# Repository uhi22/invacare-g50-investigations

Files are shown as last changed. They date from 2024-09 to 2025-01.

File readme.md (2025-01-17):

# Invacare G50 Investigations

Investigating an electric wheel chair

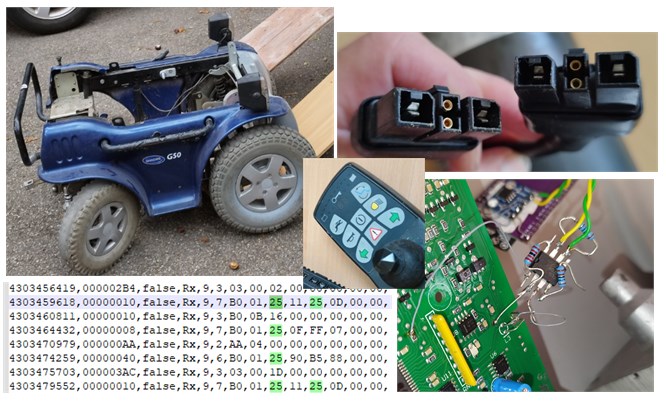
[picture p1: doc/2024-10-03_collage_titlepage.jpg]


## Progress

### 2025-01-07: DX-DASH Generation 2 ready for testing

The DX-DASH generation 2 consists of a board containing an STM32 controller, designed in KiCad,
a housing designed in FreeCad and the software designed in the STM CubeIDE.
The DX-DASH gen2 is controlling the Power Module, using either joystick or drive pedal and
direction switch.

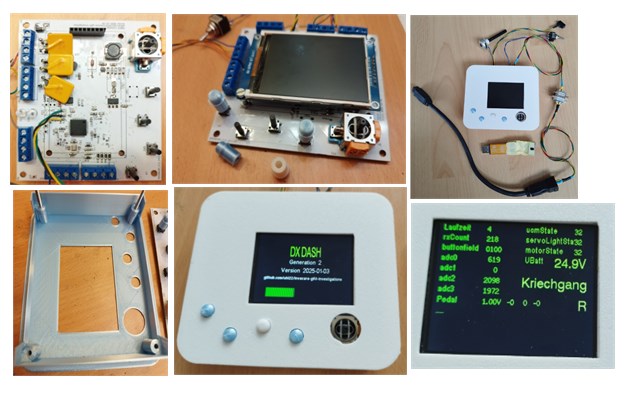
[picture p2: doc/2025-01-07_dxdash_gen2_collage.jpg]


[Instruction manual](doc/2025-01-06_DXDASH_installation_und_bedienung.md)

### 2024-10-15: STM32 simulates the UCM and the SLM

Simulating the UCM and the ServoLightModule, the STM32 is able to control
the motor speed directly.

### 2024-10-11: STM32 as UCM-replacement controls all functionality

The STM32 as UCM replacement controls a lot of functionality:
- Wakeup the other modules via the DXBUS
- Control the low beam light and the flashers
- Switch the power module into driving mode and back to idle mode
- Drive motor forwards and backwards using analog joystick input
- Turn the steering servo left and right using analog joystick input
- Send the power module and servo light module to sleep

### 2024-10-02: First spin

The STM32 sends all CAN messages to make the motor spin.

### 2024-09-30: Steering reacts

By sending some half-way proper CAN messages from the STM32 UCM replacement, the servo can be controlled to right-turn.
The motor disables the brake, but does not spin yet. It blinks 12 times.

### 2024-09-26: Controlling the lights works

Using the STM32 "blue pill" and a CAN transceiver, we control the lights via CAN. Due to the disconnected UCM,
the motor controller is stuck in state 0C, and the ServoLightModule in state 0. But nevertheless, low beam and
the turn indicators can be perfectly controlled with a 20ms message "0x040 B0 14 xx".
The ServoLightModule works even with very low battery voltage of 10V in this situation.

### 2024-09-24: STM32 interprets some network variables

Using the STM32 and attached display, we decode some network variables out of the CAN messages,
and show them on the display. 

## Goals

1. Understand the communication on the DX-BUS
2. Replace the original joystick ("UCM") by a self-made box which can control the motor, the lights and the steering.
3. Replace the UCM and the ServoLightModule by a self-made box to control only the motor.

## Pinout of the Power Module

The "Power Module" is a DX-PMB2-SAS, producer "Dynamic Controls", this seems to be the same as the DX-PMB2 mentioned in Ref1.

## Bus Communication

The "DXBUS" consists of four pins:
* Ground
* 24V
* CANH
* CANL

The ground and 24V are directly connected to the battery pins of the power module.

CAN bit time is 9.5µs, this means the CAN baud rate is 105.26 kBaud.
This baud rate can be created (according to STM32 cube IDE) with prescaler=57, T1=3, T2=2, SJW=1, TQ=1583.3ns, bittime=9500ns, 6 TQ per bit, inputClock=36MHz.

### CAN messages

UCM transmit messages (found by adding a separate CAN transceiver to the UCMs CAN_TX line):

* 0x040: The main data message. Contains lot of different sub-data.
* 0x0AA: not very interesting. Always "AA 04".
* 0x29C: "03 00 1A" during run. While turning off, "03 00 10".
* 0x2B4: Constant besides a toggle bit
* 0x2BC: nearly constant, only the last byte changes sometimes.
* 0x3A4: nearly constant, only the last byte changes during shutdown.
* 0x3AC: constant "03 00 1D"

ServoLightingModule transmit messages (found by adding a separate CAN transceiver to the ServoLightingModule CAN_TX line):

* 0x010 is the only transmit message. It contains various sub-messages, e.g.
    * 30 08 00 01 after startup
    * "B0 01 00" and "B0 01 02"
    * "10 00 ....", "12 00 ..."
    * and more

MotorModule transmit messages (all remaining messages which do not come from UCM and ServoLightingModule)
* 0x008 is the only transmit message. It contains various sub-messages, e.g.
    * A3, A1, A4 after startup
    * B0 01 02
    * B0 01 10 0F ...
    * B0 01 10 0C ...
    * B0 01 20 ...
    * B0 01 22
    * B0 01 25 
    * B0 0E ...
    * 30 02 ...
    * and more

```
0x008 B0 01 20 0C B5 0F FF
                   |
                   depends on the supply voltage. A7=22V, B6=24V, C6=26V. 150=19.8V, 200=26.5V 

0x040 B0 93 E1 00 14 00
                      |
                      lights 00=off, 11=light, 02/22 blinker right, 04/44 blinker left, 08/88 hazard flashing

0x040 B0 01 25 90 FF 80
                   |  |
                   |  joystick left/right. 01 is full left. 80 is middle. FF is full right.
                   joystick up/down. 01 is full backwards. 80 is middle, FF is full forward.
                   
0x2B4 03 00 0A
             |
             different values: 02, 0A. And 00 before power-off.

0x2BC 03 00 0F
             |
             different values: 0B, 0F. And 01 before power-off.
```

#### Message types

- First byte B0: "Network Variable announcement". After the B0 there is one byte NV_ID, followed by the content of the
network variable. The length depends on the ID. Afterwards, more {NV_ID, value} pairs may follow as long as there is space left in the CAN frame.
It is confirmed, that the same network variable can be on different position: The light control variable 14 works for controlling the lights in
the following frames in the same way:
    * 0x040 B0 93 E1 00 14 11
    * 0x040 B0 14 11

- First byte 30: "Wanna know". A node sends this message, to request network variable from other nodes.
```
   I'm the motor and...
   |   I wanna know...
   |   |  from node 2 (ServoLightModule)...
   |   |  |     the network variable 11
   |   |  |     |
0x008 30 02 00 11
```
The addressed node responds accordingly with the value of the requested network variable:
```
   I'm the ServoLightModule and...
   |   I want to announce my network variable...
   |   |  number 11...
   |   |  |   has the value 10.
   |   |  |  |
0x010 B0 11 10
```

After the variable number in the "30" message, there is sometimes more data, sometimes not. E.g. "03". Unclear: Is this an additional
network variable number? Or is it a kind of "request type" which selects the cycle time or number of responses or on/off?

- First byte 31: "unsubscribe". Tells the addressed note that it does not need to send the network variable anymore. E.g.
```
   I'm the ServoLightModule and...
   |   I do not need...
   |   |  from node 8 (UCM)...
   |   |  |     the network variable 2E
   |   |  |     |
0x010 31 08 00 2E
```
After this unsubscription, the UCM stops the cyclic transmission of NV 2E.

- First byte 20: unclear. Used in the first messages after startup. 4297725430,00000040,false,Rx,9,8,20,00,00,08,00,00,00,00,
- First byte 23: unclear. E.g. 00000040,false,Rx,9,8,23,00,00,08,FC,80,00,00. Responded by A3.
- First byte 21: similar to 23
- First byte 24: similar to 23

Request-response:
* 4297804953,00000040,false,Rx,9,8,23,00,00,08,FC,80,00,00,  request from the UCM
* 4297805609,00000008,false,Rx,9,1,A3                        response from Motor, where A3 seems to be the response to 23
* 4297806161,00000010,false,Rx,9,1,A3                        response from Servo, where A3 seems to be the response to 23
(and repeated)

again with other number:
* 4297818227,00000040,false,Rx,9,8,21,00,00,08,FC,80,00,00,  request from the UCM
* 4297818888,00000008,false,Rx,9,1,A1                        response from Motor
* 4297819437,00000010,false,Rx,9,1,A1                        response from Servo
(and repeated)

again with other number:
* 4297830564,00000040,false,Rx,9,8,24,00,00,08,FC,40,00,00,  request from the UCM
* 4297832560,00000008,false,Rx,9,1,A4                        response from Motor
* 4297832579,00000010,false,Rx,9,1,A4                        response from Servo
(and repeated)

### Profile changes

If the user changes the driving profile ("gear"), e.g. from 2 to 3, this results in
1. 040: B0,93,63,00,14,00 (once) The UCM announces profile 3.
2. 040: B0,93,E3,00 (repeated each 200ms) The UCM announces profile 3 in an other way.
3. 010: 30,08,00,2C The servo light module requests from the UCM the NV 2C.
4. 040: B0,93,E3,00,14,00,2C,66 UCM provides the NV 2C. Repeated after 200ms.
5. 010: 31,08,00,2C The servo light module stops the subscription of NV 2C.
6. The request/response/unsubscribe continues for other variables.

The end speed (at full joystick way) is parametrized separately for forward and reverse directions. Example profiles,
to demonstrate the speed influence of NV 2C (forward speed) and NV 2F (reverse speed):

```
		/* profiles:
		  1     2     3     4     5  */
		0x10, 0x59, 0x66, 0x73, 0xff, /* NV 0x2C */ /* max speed fwd. 10=very low, ff=high speed */
		0x66, 0x66, 0x73, 0x80, 0x80, /* NV 0x2D */
		0x20, 0x80, 0x80, 0x80, 0x80, /* NV 0x2E */
		0x10, 0x66, 0x66, 0x66, 0xff, /* NV 0x2F */ /* max speed reverse. 10=very low, ff=high speed */
		0x66, 0x66, 0x73, 0x80, 0x80, /* NV 0x30 */
		0x99, 0x99, 0x99, 0x99, 0x99, /* NV 0x31 */
		0xCC, 0xCC, 0xCC, 0xCC, 0xCC, /* NV 0x32 */
		0xB3, 0xB3, 0xB3, 0xB3, 0xB3, /* NV 0x33 */
		0x33, 0x33, 0x4D, 0x4D, 0x4D, /* NV 0x34 */
		0x80, 0x80, 0x99, 0xA6, 0xA6, /* NV 0x35 */
```

These profiles are used only by the ServoLightModule. The motor module is not interested into these profiles. The motor
module is controlled by network variable 0B, which the ServoLightModule provides.

### Error Codes

The PowerModule provides with the network variable 07 some error information:
- 00: no error. No blink code on the UCM.
- 0C: uncoupled the G40 motor. Blink code 3 on the UCM.
- 10: Motor M1 disconnected. Blink code 5 on the UCM.
- (more to be tested)

To use this error reporting, the NV 07 needs to be requested once at the beginning:
`00000010,false,Rx,9,4,30,01,00,07`

## The Wakeup

As long as the system is "off", the DX-BUS still carries 24V battery voltage, and both CAN lines are sitting at ~2.5V.
The system is activated when the user pushes the on/off button on the joystick module ("UCM"). The UCM wakes the other
control units by pulling the CANH to 24V for ~40ms. Afterwards, the UCM sends CAN traffic to keep the other control units
awake. If we apply just the wakeup pulse and do not send any CAN messages, the control units go to sleep again after five seconds.

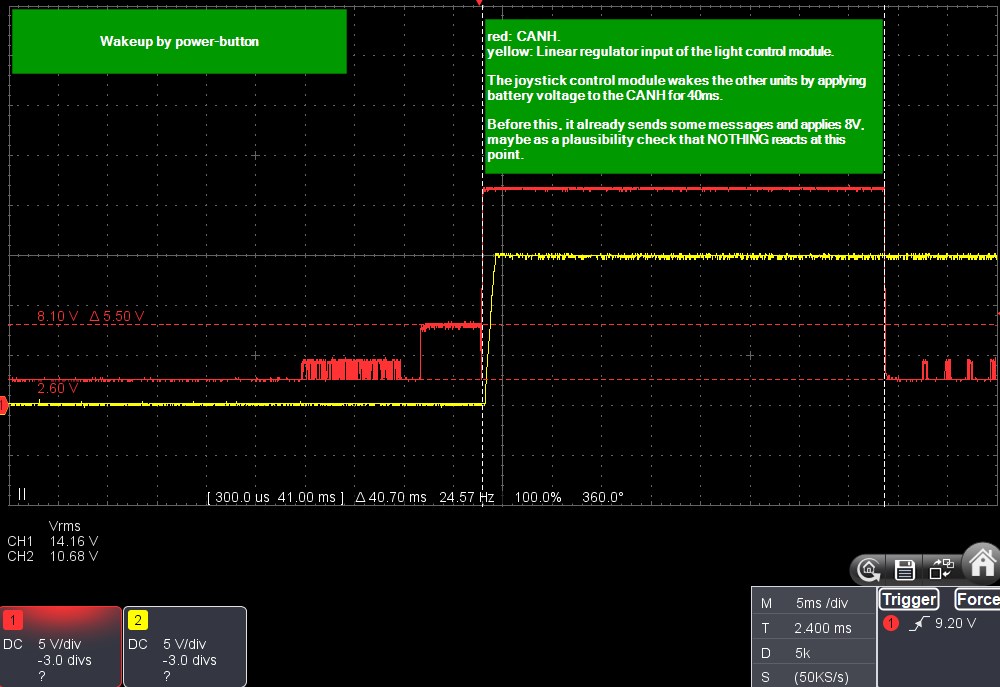
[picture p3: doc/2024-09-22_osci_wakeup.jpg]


## The Go-To-Sleep

If the user pushes the on/off button while the system is running, the UDS sends some special messages to send the other control
units to sleep, and stops the CAN communication. (Todo: Details to be described.)
If we just stop sending any messages from the UCM, the ServoLightModule enters an "emergency mode" after some seconds, where
it activats the hazard-flashing.

## Using the ServoLightModule standalone

The ServoLightModule can be used without the PowerModule to control the lights and the steering servo. Several aspects need to be considered to make this work.

1. The CAN termination. The absence of the PowerModule causes a missing CAN termination. We need to add a 510 ohm (or 470ohm) between
CANH and CANL. Additionally, we need a pull-up of the CANH via a diode and 390ohms (in series) to 3.3V, because the CAN transceiver inside
the SLM seems not to be capable of driving the CANH to high; it only pulls the CANL to low. So without additional pull-up on CANH,
a normal CAN transceiver is not able to pick-up the messages of the SLM.

2. The light control. This is the easy part. The SLM listens to the network variable 0x14, which we can announce e.g. with a message `0x040 B0 93 E1 00 14 00`. The light control bits are explained above. The SLM does not need to see the PowerModule for this functionality.

3. The steering servo control. This part is more tricky. To make the steering function work, the SLM needs to see the PowerModule and needs
to go through the corrects states.

    - The UCM and PowerModule must simulate the 23/A3, 21/A1 and 24/A4 sequences during startup.
    - The PowerModule must send the status after the SLM requests it with 010 30 01 00 01.
    - The PowerModule must send the network variables 0F, 0E and 07 after the SLM requested it with 010 30 01 00 0F or 010 30 01 00 0E or 010 30 01 00 07. If the SLM does not receive them, it changes from state 10 (init) to state 0C (error).
    - Even if the SLM now removes the steering brake when entering state 0x25, still the steering only works sporadically. To be further investigated.

## UCM (Joystick Control Module)

CAN_TX: Is the pin 1 of the 74HC02 on the sub-board.

### Diagnostic Connector

according to ref1, this is RS232.

## The Motor Controller (Power Module, PM)

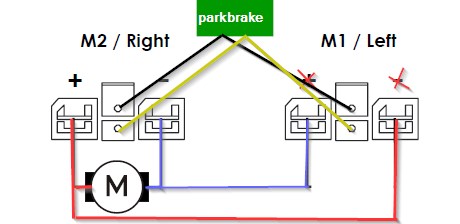
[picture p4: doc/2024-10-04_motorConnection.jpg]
Pinout: 

Motor PWM control:

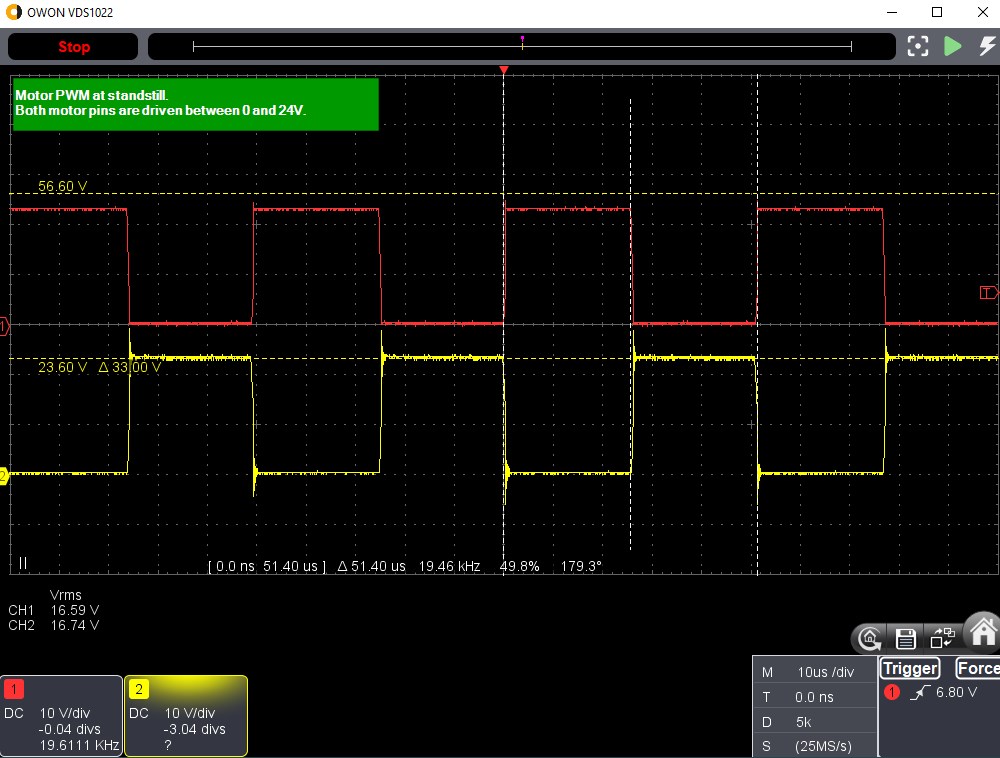
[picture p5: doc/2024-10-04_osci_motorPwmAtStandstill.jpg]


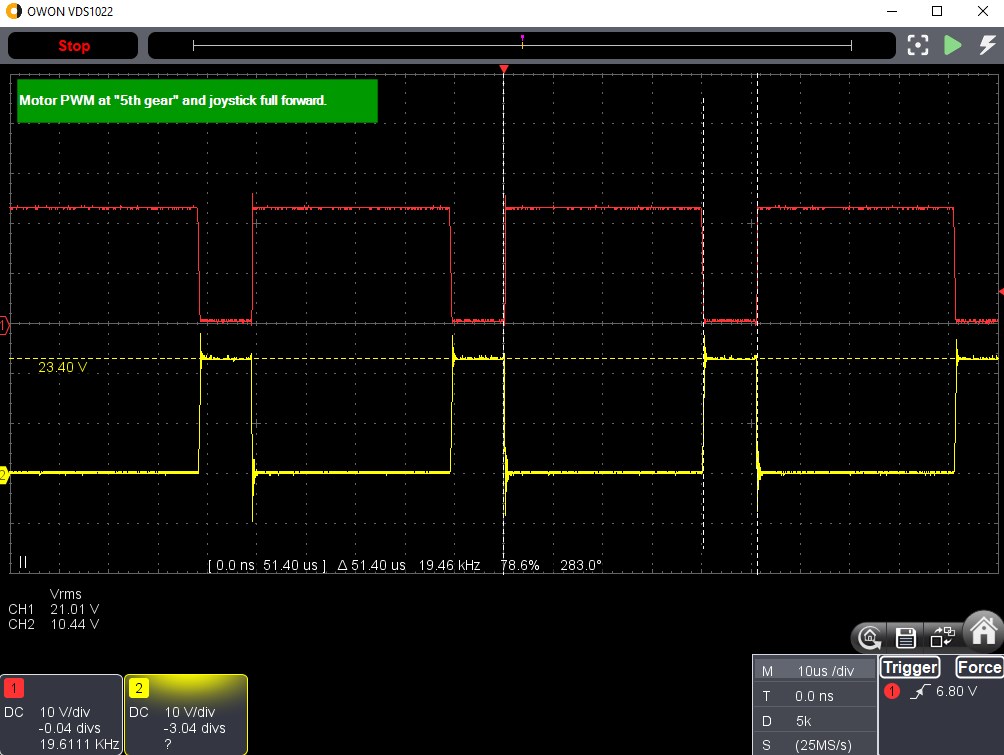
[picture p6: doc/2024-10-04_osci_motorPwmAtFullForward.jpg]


Park brake control:

* The black park brake wire is grounded.
* The yellow park brake wire is switched to 24V to release the brake. Each 200ms, the PM turns the park brake off for 250µs, most likely for diagnotic purposes.

Current consumption:

* in sleep: 600µA. This means, a 20Ah usable battery capacity lasts for more than 3 years.

## The Motor

* Does does a motor of a G40 work at the motor controller of the G50? Yes.
* How does the "manual clutch switch" work?
    * In the G50 motor, when the user actuates the clutch to push the chair manually, the motor-integrated switch disconnects the *park brake magnet*.
    * In the G40plus motor, the motor integrated switch directly disconnects the *motor*.

## Self-made DXBUS controller

An STM32 development board ("blue pill"), combined with a ILI9341 TFT display and a SN65HVD230 CAN transceiver board and some small additions
is used to send and receive the CAN messages on the DXBUS, and also to send the wakeup pulse.

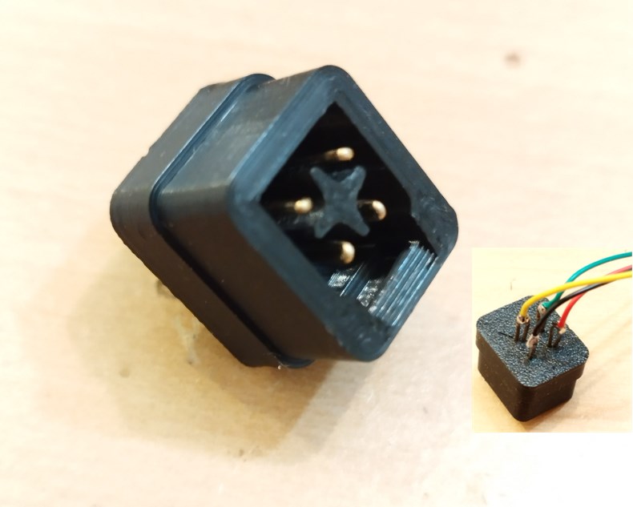
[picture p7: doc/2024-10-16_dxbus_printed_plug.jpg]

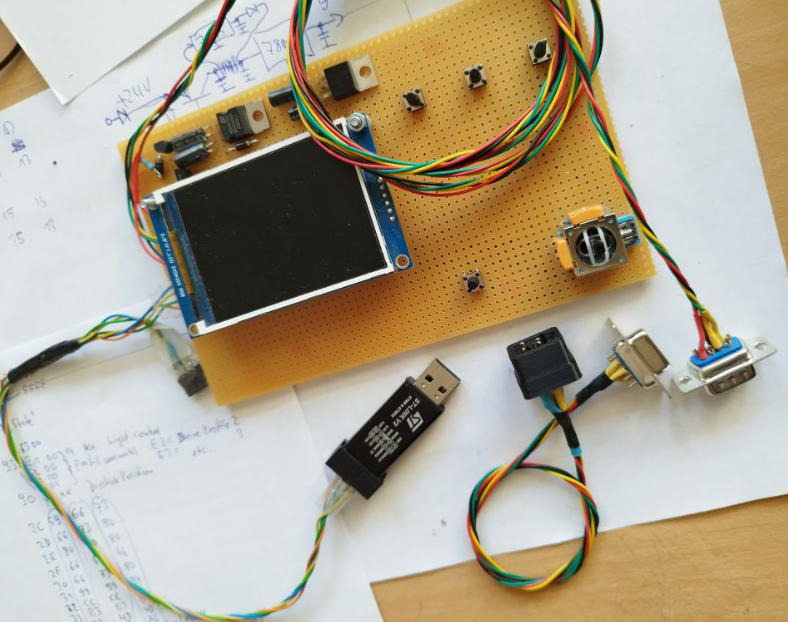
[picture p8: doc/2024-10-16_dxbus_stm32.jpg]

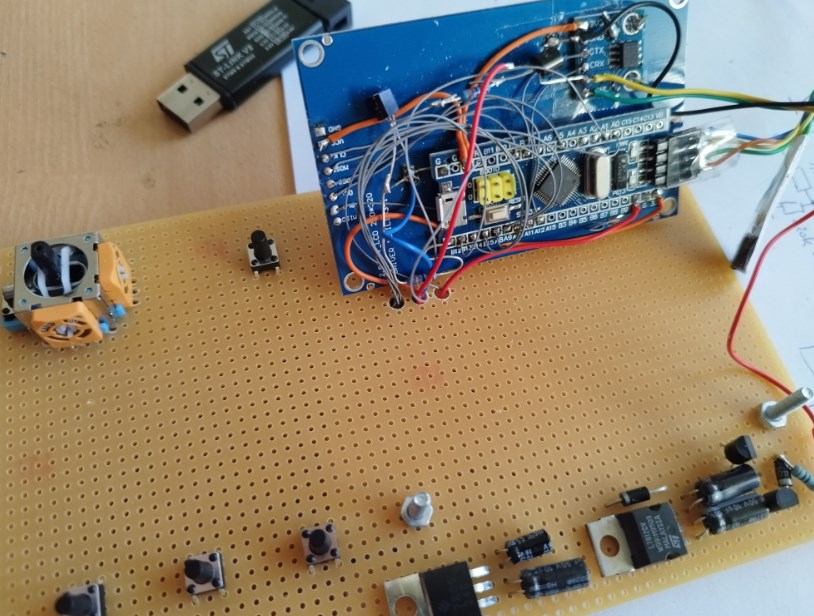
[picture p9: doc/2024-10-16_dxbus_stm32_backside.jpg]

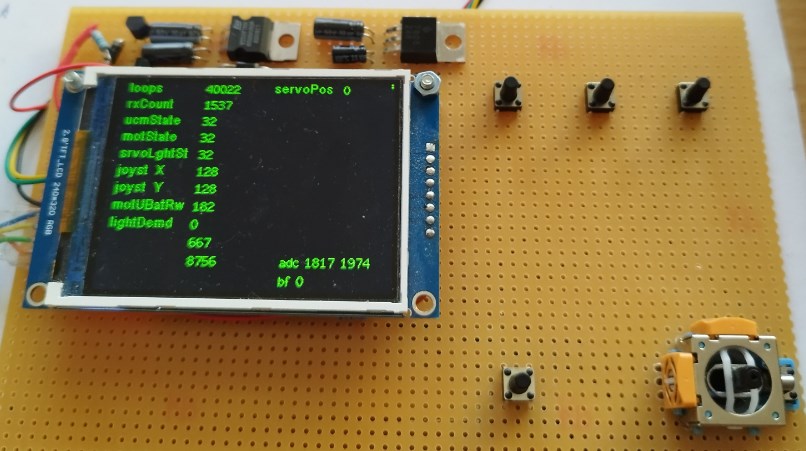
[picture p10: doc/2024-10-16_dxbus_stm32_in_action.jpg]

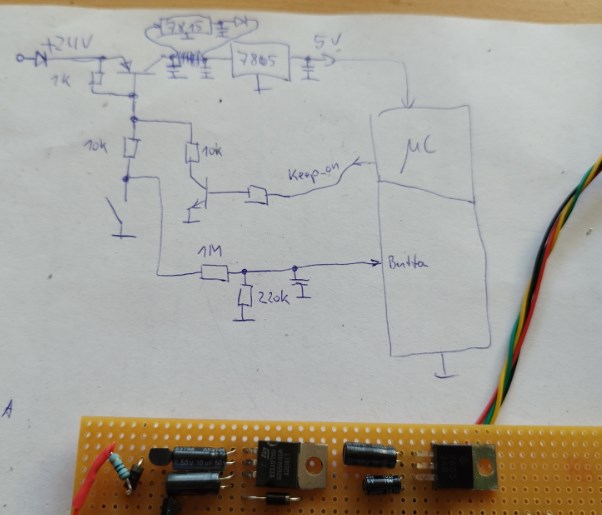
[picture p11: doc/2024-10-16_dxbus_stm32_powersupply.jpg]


The 3D model for the printed DXBUS plug is available as [FreeCad model](3d_models/DXBUS_plug.FCStd) and [step file](3d_models/DXBUS_plug.step).

The software (as STM CubeIDE project) is available [here](stm32-tft).

## Open Todos

- [ ] ServoPos shows permanent 0
- [ ] add direction switch and pedal input
- [ ] implement special case "power button during driving"
- [ ] improve CAN scheduling to avoid message losses

## Finished Todos

- [x] Send NV 92 with FF FF in 200ms cycle
- [x] Send the profile (e.g. NV 93 = E1 00)
- [x] Send the parameters of the profile (NVs 2C to 35), after the ServoLight 0x010 requested it, e.g.
    - servoLight requests the 2C from UCM with 00000010,false,Rx,9,4,30,08,00,2C
    - ...
    - servoLight requests the 2E from UCM with 00000010,false,Rx,9,4,30,08,00,2E
    - more general: UCM needs to satisfy all requests (search for 30,08,00)
- [x] Find out how to parametrize the speed
- [x] Reset the CAN controller if it enters bus-off
- [x] Implement UCM start/idle/drive/idle/shutdown state machine
- [x] implement emulation of ServoLightModule, to be able to run the motor control unit without physical ServoLightModule

## Cross References

* [Ref1] System manual for the DXBUS https://www.dynamiccontrols.com/sites/default/files/2018-05/dx-system-manual-issue1.pdf
* [Ref2] European Patent EP0725738A1 (year 1993) https://patents.google.com/patent/EP0725738A1/en
* [Ref3] European Patent EP0725738B1 (year 1993), including schematics, state machines, some network variables. https://patents.google.com/patent/EP0725738B1/en
* [Ref4] SavvyCAN open source CAN logging tool https://www.savvycan.com/
* [Ref5] wifican CAN adaptor via wifi. Adapted to support the 105kBaud of the DXBUS. https://github.com/uhi22/wifican/commit/1e717946a06a594cf2e79b092cbaf7b376e8bb55
* [Ref6] pictures and document collection for the Invacare G50 https://hnng.de/invacare-g50/
* [Ref7] Master Thesis of Markus Schuch / Technikum Wien including a good overview over different wheel chair concepts, and a raspberry-pi based CAN "man in the middle" approach for the DXBUS. https://epub.technikum-wien.at/urn/urn:nbn:at:at-ftw:1-39670

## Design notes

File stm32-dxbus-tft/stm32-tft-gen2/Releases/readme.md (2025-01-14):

# Software für DX-DASH Generation 2

## Version 2025-01-14-B

* Symbole für Blinker und Licht hinzugefügt

[download](dxdash-gen2-2025-01-14-B.hex)

## Version 2025-01-14-A

* Fehler behoben: Empfang von Netzwerkvariablen vom PowerModul, unabhängig von deren Position in der CAN-Botschaft

[download](dxdash-gen2-2025-01-14-A.hex)

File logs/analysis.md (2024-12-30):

# 2024-12-28_CAN_gen2_run_but_stopped_002.csv

872,00000010,false,Rx,9,7,B0,01,25,11,25,0D,00,00,
878,00000010,false,Rx,9,3,B0,0B,E9,00,00,00,00,00, dT 6ms
883,00000010,false,Rx,9,3,B0,0E,00,00,00,00,00,00, dT 5ms
898,00000010,false,Rx,9,3,B0,0B,E9,00,00,00,00,00, dT 15ms
918,00000010,false,Rx,9,3,B0,0B,E9,00,00,00,00,00, dT 20ms
931,00000008,false,Rx,9,4,30,02,00,11,00,00,00,00,

Observed:
- The power module (00008) requests "11" from the SLM.
- This is because the SLM misses to send the long message B0,01,25,11,25,0D,00 in the expected 20ms cycle.
Improvement: In the tx queue handling, only mark the
message as "transmitted" if it was successfully given to the HAL.

Solution: enable automatic retransmission. Otherwise messages which are
overruled by the arbitration are completely lost.

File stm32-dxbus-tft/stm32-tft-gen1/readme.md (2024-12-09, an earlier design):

# Hardware

* STM32F103C8T6 "Blue Pill"
* TFT display with ILI9341 controller

# Settings

* 8 MHz HSE
* 72 MHz SYSCLK
* 72 MHz HCLK
* 72 MHz HCLK to AHB
* 72 MHz to Cortex System Timer
* 72 MHz FCLK
* 36 MHz APB1 peri
* 72 MHz APB1 timer
* 36 MHz APB2 peri
* 72 MHz APB2 timer
* 9 MHz To ADC1,2

* CAN
    * Prescaler 57 (TQ 1583ns)
    * Seg 1: 3 times, Seg2: 2 times
    * SJW: 1 times
    * automatic bus-off recovery enabled
    * RX0 interrupt enabled
    * PA11 RX
    * PA12 TX
* SPI
    * Motorola, 8 bit, MSB first
    * Prescaler 2 (18 MBit)
    * CPOL low
    * CPHA 1 edge
    * DMA1 channel3 global interrupt enabled
    * DMA: SPI1TX : DMA1 channel 3, memory to peripheral, prio low.
    * PA5 SPI1_SCK
    * PA7 SPI_MOSI

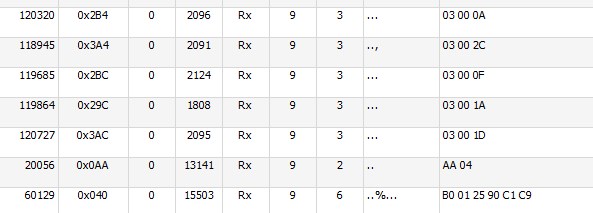
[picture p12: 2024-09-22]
doc/2024-09-22_CAN_UCM_txmessages_while_driving_forward_rightturn.jpg

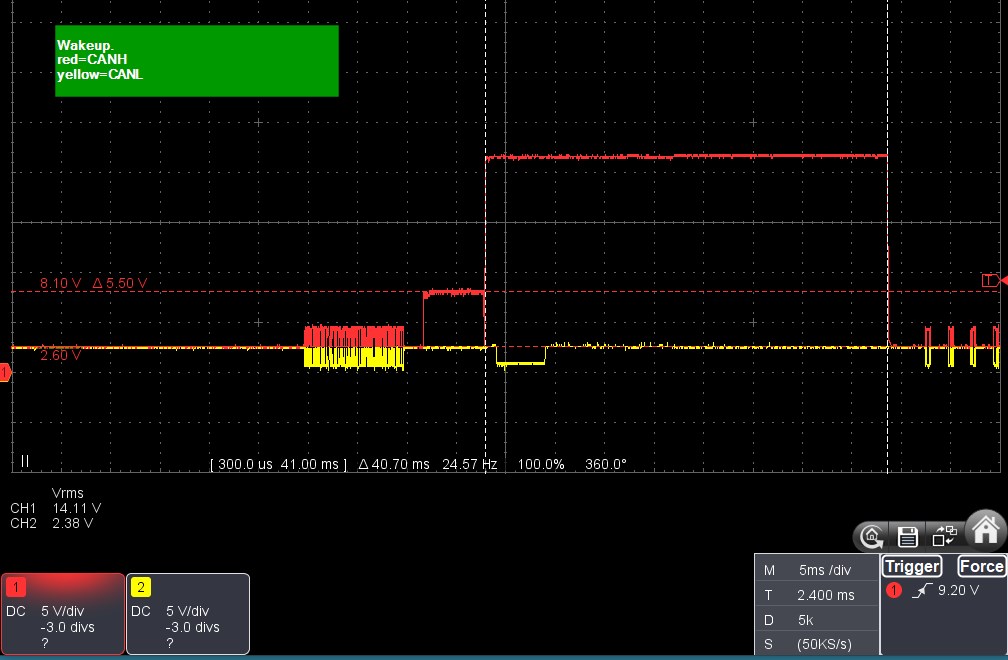
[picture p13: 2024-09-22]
doc/2024-09-22_wakeup_CANH_CANL.jpg

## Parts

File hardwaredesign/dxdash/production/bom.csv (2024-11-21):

Designator | Footprint | Quantity | Value | LCSC Part #
C1 | 1206 | 1 | 100n | C14663
C2, C3, C60, C64 | 1206 | 4 | 100nF | C14663
C56, C57, C58, C59, C61, C73, C74 | 0805 | 7 | 100nF | C14663
C62, C63 | 0805 | 2 | 22p | C1679
C65 | 1206 | 1 | 10uF | C14663
C66, C67 | 1206 | 2 | 22uF | C14663
C68 | 1206 | 1 | 68pF | C14663
C69 | CP_Elec_10x10 | 1 | 470uF
C75 | CP_Elec_8x10 | 1 | 100uF
D1, D11 | LED_D5.0mm | 2 | LED2
D10 | 0805 | 1 | ALIVE
D13 | D_SMB_Handsoldering | 1 | SS54B-HF
D15 | 0805 | 1 | UARTTX
D2 | D_DO-201_P15.24mm_Horizontal | 1 | Zener 5V
D9 | 0805 | 1 | PWR
F1, F2, F3 | Fuse_Bourns_MF-RG400 | 3 | Polyfuse
J1 | PinHeader_1x08_P2.54mm_Vertical | 1 | Conn_01x08_Pin
J10, J11, J3, J7, J9 | TerminalBlock_Phoenix_MKDS-3-4-5.08_1x04_P5.08mm_Horizontal | 5 | Screw_Terminal_01x04
J13 | PinHeader_1x01_P2.54mm_Vertical | 1 | Conn_01x01_Pin
J16 | PinHeader_1x01_P2.54mm_Vertical | 1 | uC_NRST
J17 | PinHeader_1x01_P2.54mm_Vertical | 1 | 3V3_uC
J18 | PinHeader_1x01_P2.54mm_Vertical | 1 | SWO
J4 | PinHeader_1x03_P2.54mm_Vertical | 1 | DEBUG
J5 | PinHeader_1x03_P2.54mm_Vertical | 1 | UART
L12 | 0805 | 1 | Bead 600 | C1002
L13 | L_Wuerth_WE-PD-Typ-LS_Handsoldering | 1 | 10uH | C162588
Q1, Q2, Q3 | SOT-223 | 3 | NCV8402xST
Q4, Q7 | TO-92_Inline | 2 | BC556
Q6, Q8 | TO-92_Inline | 2 | BC546
R1, R13, R29, R3, R30, R32, R33, R35, R36, R43, R45, R5 | 1206 | 12 | 10k | C25804
R10, R7, R9 | 1206 | 3 | 4k7 | C22978
R11, R12, R4, R6, R8 | 1206 | 5 | 10k | C22978
R14, R16, R25, R26, R27, R28, R34, R39, R40, R42, R44, R46 | 1206 | 12 | 47k | C25804
R15 | 1206 | 1 | 33 | C23140
R17, R18, R19, R2, R20, R37 | 1206 | 6 | 1k | C22978
R21, R22 | 1206 | 2 | 220 | C22978
R23 | 1206 | 1 | 100k | C25804
R24 | 1206 | 1 | 33k | C25804
R31 | joystickXYButton | 1 | Joystick
R38 | 1206 | 1 | 22k | C25804
R41 | 1206 | 1 | 100
SW1, SW2, SW3, SW4, SW5 | SW_PUSH_6mm_H5mm | 5 | SW_Push
TP1, TP10, TP11, TP2, TP21, TP22, TP25, TP26, TP27, TP28, TP29, TP33, TP7, TP8, TP9 | TestPoint_THTPad_D1.0mm_Drill0.5mm | 15 | ~
TP5V1 | TestPoint_THTPad_D1.0mm_Drill0.5mm | 1 | TP5V
U2 | SOIC-8_3.9x4.9mm_P1.27mm | 1 | SN65HVD234
U3 | LQFP-64_10x10mm_P0.5mm | 1 | STM32F103RETx
U4 | SOT-23-6 | 1 | TPS54302
U6 | SOT-223-3_TabPin2 | 1 | AMS1117-3.3
U7 | SO-14_3.9x8.65mm_P1.27mm | 1 | 74HCT04
Y2 | Crystal_SMD_TXC_7M-4Pin_3.2x2.5mm | 1 | 8MHz | tbd

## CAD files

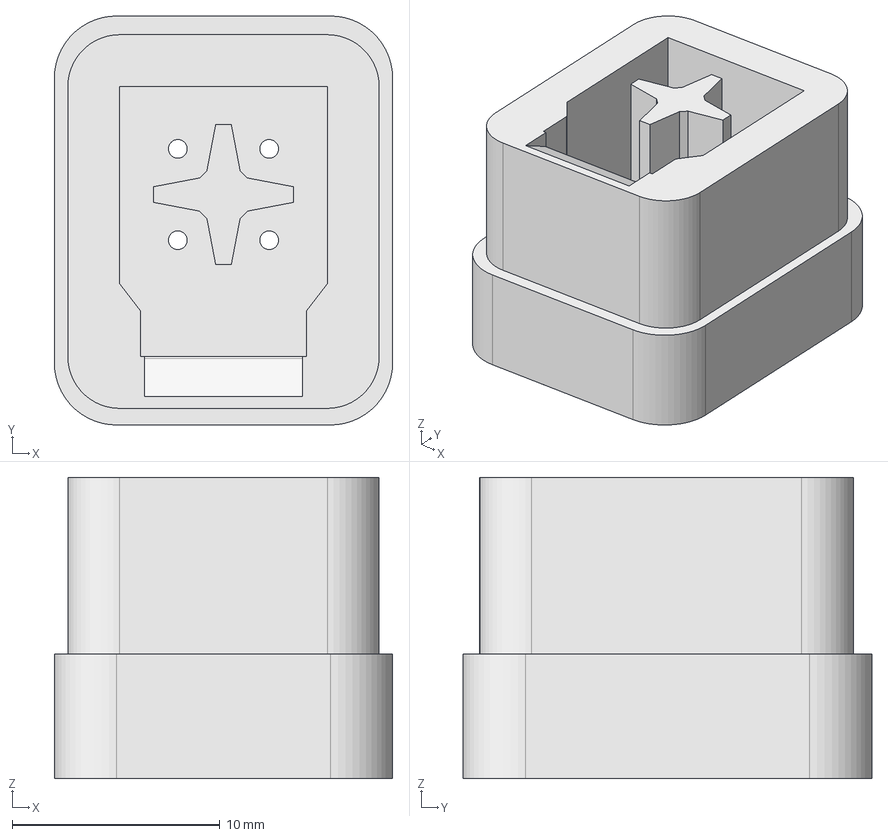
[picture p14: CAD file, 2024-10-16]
3d_models/DXBUS_plug.step
16.3 x 19.7 x 14.5 mm

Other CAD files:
3d_models/DXBUS_plug.FCStd

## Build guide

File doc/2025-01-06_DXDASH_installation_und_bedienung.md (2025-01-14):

# DX-DASH Installations- und Bedienungsanleitung

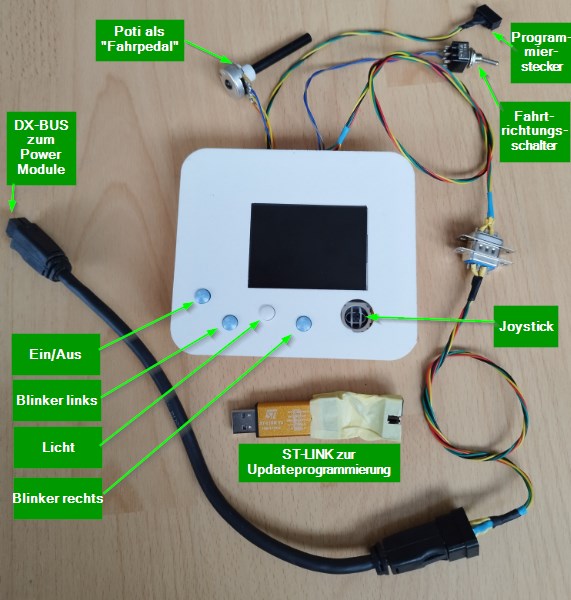
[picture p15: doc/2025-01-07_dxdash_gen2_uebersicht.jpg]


## Verwendungszweck

Das DX-Bus-Dashboard (kurz: DX-DASH) in der Version "Generation 2, Software 2025-01-06" dient zur
Ansteuerung eines Motorsteuergerätes (Power Module DX-PMB-SAS) über den DX-BUS. Es ersetzt die
Busteilnehmer "Joystick-Modul" (UCM, Universal Control Module) und "Servo Lighting Module" (Steuergerät
für Lenkservo und Beleuchtung). 

## Installation

### DX-BUS

Das DX-DASH wird mit dem Power Module über den vierpoligen DX-BUS verbunden. Das Power Module liefert
auf dem DX-BUS permanent 24V. Das DX-DASH wird vom DX-BUS versorgt. Die Kommunikation und das
aufwecken / einschlafen läuft über die CAN-Leitungen vom DX-BUS.
Der DX-BUS wird am DX-DASH an folgenden Klemmen angeschlossen:

* 24V (Batterie plus, abgesichert im Power Module)
* GND (Batterie minus über Power Module)
* CANH (CAN-Bus, high)
* CANL (CAN-Bus, low)

### Beleuchtung

Das DX-DASH hat drei Leistungsausgänge zur Ansteuerung von Glühlampen: Blinker links, Blinker rechts und Fahrlicht.
Die Glühlampen werden zwischen 24V (entweder vom Akku über separate Sicherung, oder vom 24V-Anschluss des DX-BUS) und den Ausgang geschaltet. Das DX-DASH schaltet den Ausgang auf GND (also Batterie-Minus) durch.
Die Leistungsausgänge sind im DX-DASH über selbstheilende Sicherungen mit ca. 3A abgesichert.
Die Klemmen am DX-DASH sind:

* OUT 1
* OUT 2
* OUT 3

### Fahrpedal

Das DX-DASH ermöglicht den Anschluss eines Fahrpedals, welches zwei unabhängige Potentiometer enthält.
In der aktuellen Version wird lediglich ein Potentiometer ausgewertet.
Das DX-DASH versorgt die Potentiometer mit 5V, und liest die Spannungen der Schleifer ein.
Das DX-DASH erwartet am Kanal 1 eine Spannung zwischen 1V (Pedal vollständig losgelassen) bis 4V (Pedal vollständig durchgetreten).
Die Klemmen am DX-DASH am Steckverbinder J10 sind:

* POT5V: 5V Versorgung für die Potis
* GND: Minusanschluss der Potis
* 1: Schleifer vom Poti 1
* 2: Schleifer vom Poti 2

### Fahrtrichtungsauswahl

Das DX-DASH liest einen Schalter ein, um die Fahrtrichtung (vorwärts/rückwärts) auszuwählen.

Der Schalter wird angeschlossen an:
* SWT1
* GND

### Software-Update

Zum Software-Update wird ein ST-LINK-Programmieradapter verwendet, um den Programmierstecker vom
DX-DASH mit einem USB-Anschluss des PCs zu verbinden.

Es gibt verschiedene Wege, das Update durchzuführen:

1. Kommandozeile: `$ ST-LINK_CLI -P dxdash-gen2.hex`. Das Tool ist enthalten z.B. in den STM32-Arduino-Tools, downloadbar von https://github.com/rogerclarkmelbourne/Arduino_STM32 über den Button "Code" und "Download ZIP". Nach dem Entpacken liegt es in Downloads/Arduino_STM32-master/Arduino_STM32-master/tools/win/stlink/st-link_cli.exe

2. Nutzeroberfläche: Die Installation ist hier beschrieben: https://www.st.com/en/development-tools/stsw-link004.html

Während des Updates muss der Einschaltknopf am DX-DASH dauerhaft gedrückt bleiben, um eine
durchgehende Spannungsversorgung sicherzustellen.
Falls ein Update fehlschlägt, ist das kein Problem. Es können problemlos weitere Updates (auf gleiche und andere
Software-Versionen) durchgeführt werden.

Die Software-Dateien (mit der Endung .hex) können heruntergeladen werden von https://github.com/uhi22/invacare-g50-investigations/tree/main/stm32-dxbus-tft/stm32-tft-gen2/Releases

## Bedienung

- Ein- und Ausschalten: Linker Knopf
- Blinker links: unterer linker Knopf
- Blinker rechts: unterer rechter Knopf
- Fahrlicht: mittlerer Knopf
- Warnblinken: beide Blinkerknöpfe gleichzeitig drücken
- Fahren über Joystick: Joystick nach oben oder unten betätigen.
- Fahren über Fahrpedal: Fahrtrichtung mittels Fahrtrichtungsschalter auswählen und Fahrpedal betätigen
- Wechsel von Kriechgang zu Schnellgang: Joystick für eine Sekunde nach rechts betätigen
- Wechsel von Schnellgang zu Kriechgang: Joystick für eine Sekunden nach links betätigen

### Fehlermeldungen

Das DX-DASH zeigt Fehlermeldungen als roten Balken mit Fehlernummer und Fehlertext an.
Die meisten dieser Fehler erfordern zur Behebung einen Neustart. Dazu das DX-DASH ausschalten,
fünf Sekunden warten und wieder einschalten.

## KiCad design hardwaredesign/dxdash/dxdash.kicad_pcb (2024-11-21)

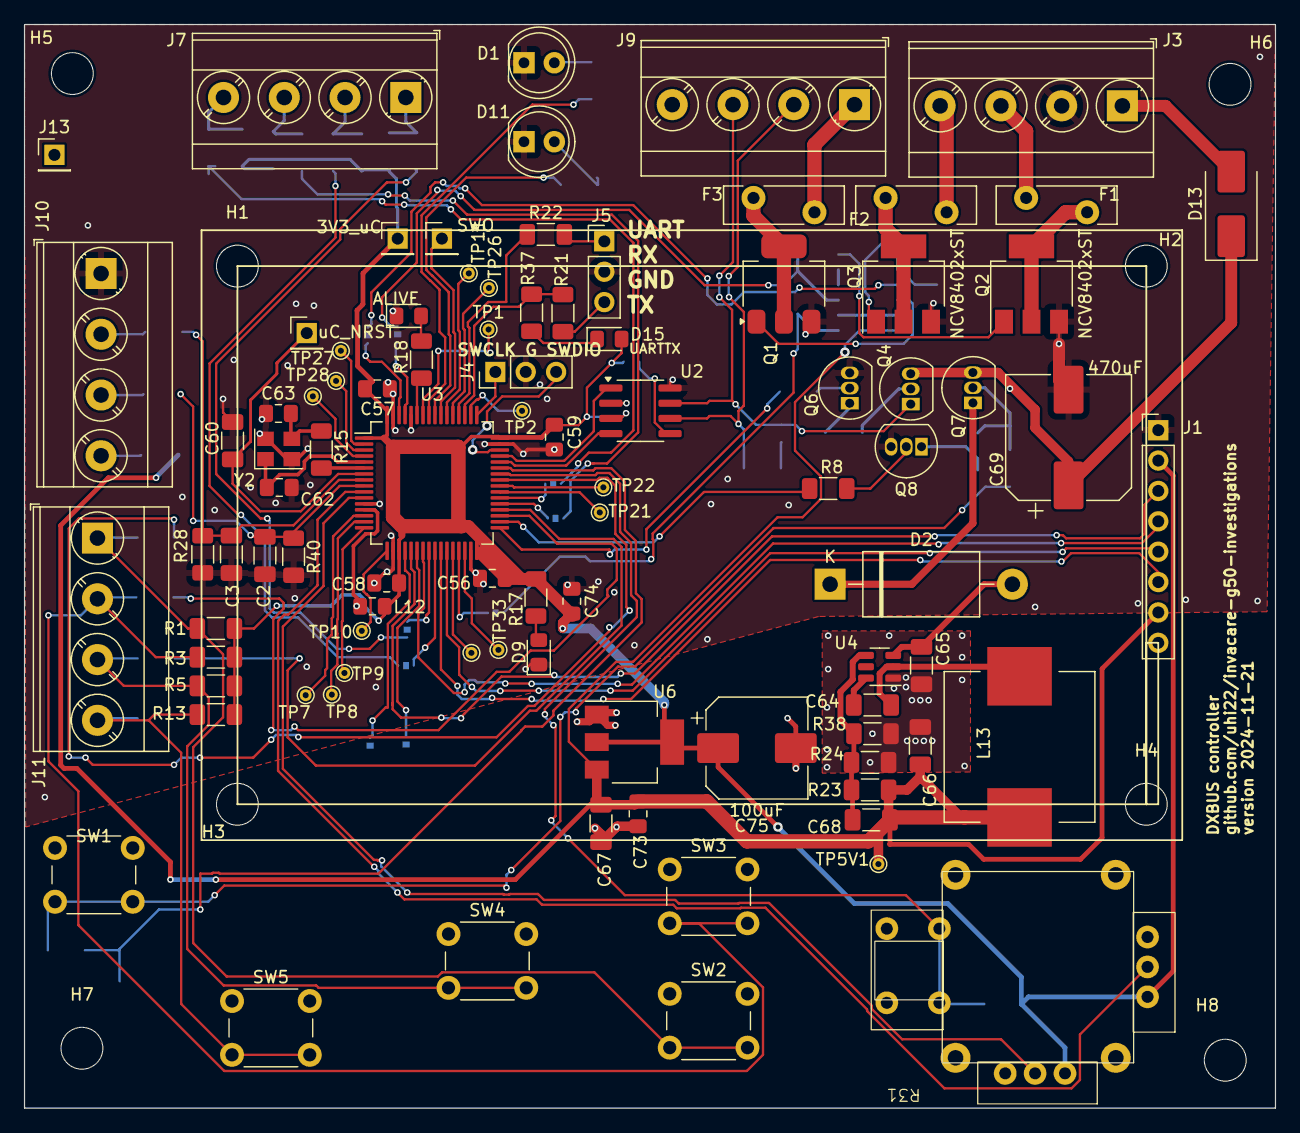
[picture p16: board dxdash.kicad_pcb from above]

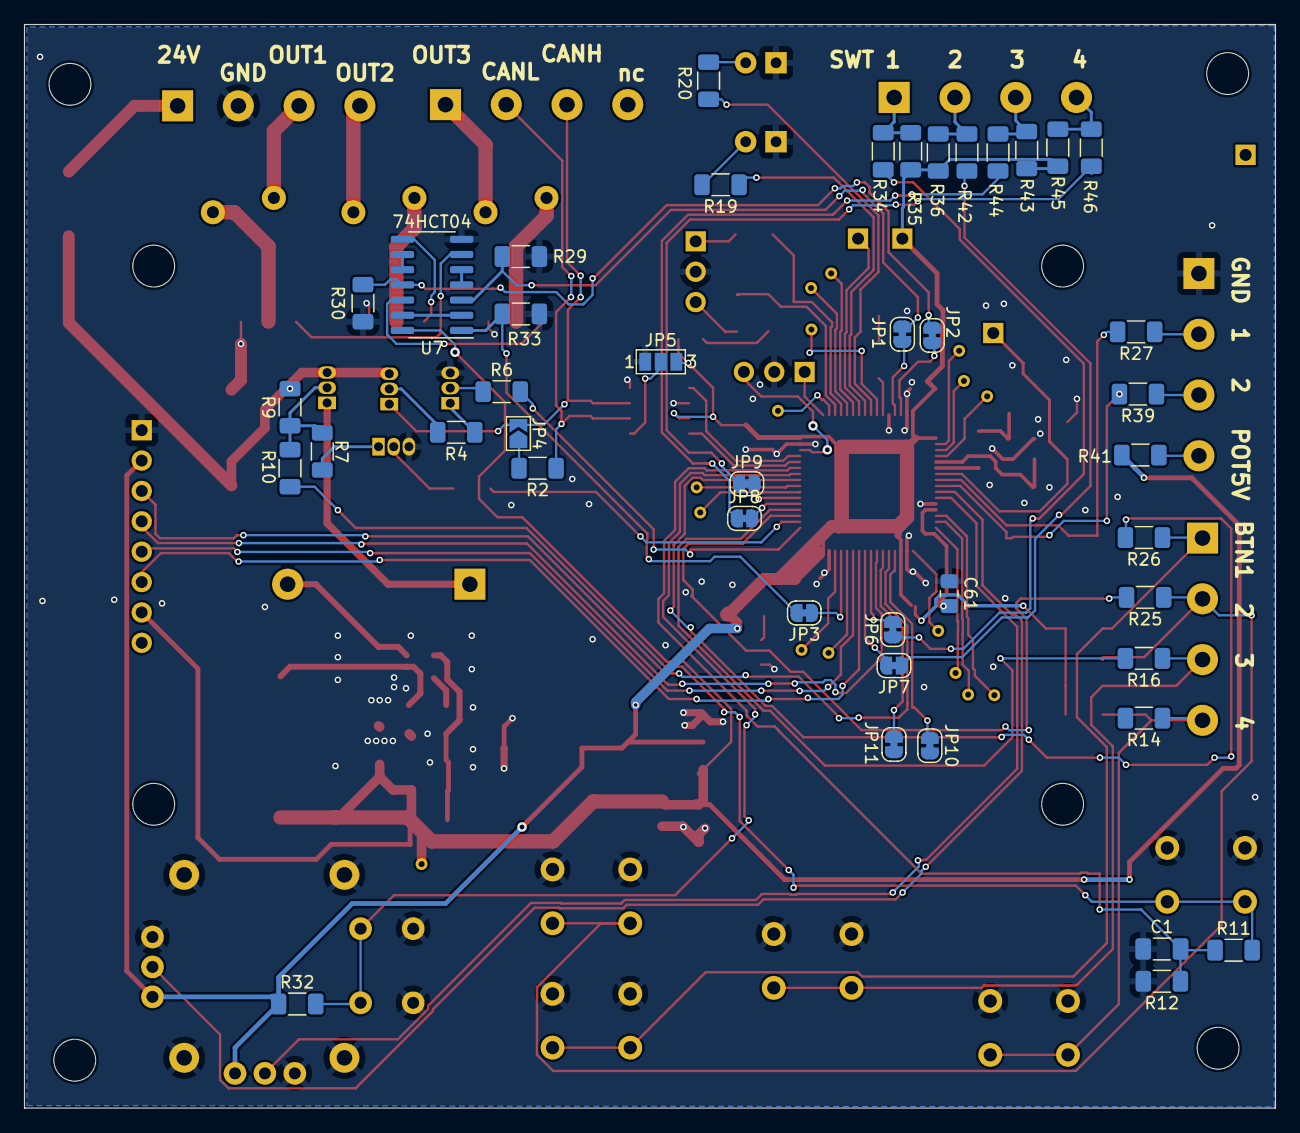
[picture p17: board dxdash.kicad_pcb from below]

Board: 2 copper layers, 104.6 x 90.6 mm, 143 parts (43 on the bottom side), 112 nets.

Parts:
C1: 100n; C_1206_3216Metric_Pad1.33x1.80mm_HandSolder
C2, C3, C60, C64: 100nF; C_1206_3216Metric_Pad1.33x1.80mm_HandSolder
C56, C57, C58, C59, C61, C73, C74: 100nF; C_0805_2012Metric_Pad1.18x1.45mm_HandSolder
C62, C63: 22p; C_0805_2012Metric_Pad1.18x1.45mm_HandSolder
C65: 10uF; C_1206_3216Metric_Pad1.33x1.80mm_HandSolder
C66, C67: 22uF; C_1206_3216Metric_Pad1.33x1.80mm_HandSolder
C68: 68pF; C_1206_3216Metric_Pad1.33x1.80mm_HandSolder
C69: 470uF; CP_Elec_10x10
C75: 100uF; CP_Elec_8x10
D1, D11: LED2; LED_D5.0mm
D2: Zener 5V; D_DO-201_P15.24mm_Horizontal
D9: PWR; LED_0805_2012Metric_Pad1.15x1.40mm_HandSolder
D10: ALIVE; LED_0805_2012Metric_Pad1.15x1.40mm_HandSolder
D13: SS54B-HF; D_SMB_Handsoldering
D15: UARTTX; LED_0805_2012Metric_Pad1.15x1.40mm_HandSolder
F1, F2, F3: Polyfuse; Fuse_Bourns_MF-RG400
H1, H2, H3, H4, H5, H6, H7, H8: MountingHole; MountingHole_3.5mm
J1: Conn_01x08_Pin; PinHeader_1x08_P2.54mm_Vertical
J3, J7, J9, J10, J11: Screw_Terminal_01x04; TerminalBlock_Phoenix_MKDS-3-4-5.08_1x04_P5.08mm_Horizontal
J4: DEBUG; PinHeader_1x03_P2.54mm_Vertical
J5: UART; PinHeader_1x03_P2.54mm_Vertical
J13: Conn_01x01_Pin; PinHeader_1x01_P2.54mm_Vertical
J16: uC_NRST; PinHeader_1x01_P2.54mm_Vertical
J17: 3V3_uC; PinHeader_1x01_P2.54mm_Vertical
J18: SWO; PinHeader_1x01_P2.54mm_Vertical
JP1, JP2, JP3, JP6, JP7, JP8, JP9, JP10, JP11: SolderJumper_2_Bridged; SolderJumper-2_P1.3mm_Bridged_RoundedPad1.0x1.5mm
JP4: SolderJumper_2_Open; SolderJumper-2_P1.3mm_Open_TrianglePad1.0x1.5mm
JP5: SolderJumper_3_Open; SolderJumper-3_P1.3mm_Open_Pad1.0x1.5mm_NumberLabels
L12: Bead 600; L_0805_2012Metric_Pad1.15x1.40mm_HandSolder
L13: 10uH; L_Wuerth_WE-PD-Typ-LS_Handsoldering
Q1, Q2, Q3: NCV8402xST; SOT-223
Q4, Q7: BC556; TO-92_Inline
Q6, Q8: BC546; TO-92_Inline
R1, R3, R4, R5, R6, R8, R11, R12, R13, R29, R30, R32, R33, R35, R36, R43, R45: 10k; R_1206_3216Metric_Pad1.30x1.75mm_HandSolder
R2, R17, R18, R19, R20, R37: 1k; R_1206_3216Metric_Pad1.30x1.75mm_HandSolder
R7, R9, R10: 4k7; R_1206_3216Metric_Pad1.30x1.75mm_HandSolder
R14, R16, R25, R26, R27, R28, R34, R39, R40, R42, R44, R46: 47k; R_1206_3216Metric_Pad1.30x1.75mm_HandSolder
R15: 33; R_1206_3216Metric_Pad1.30x1.75mm_HandSolder
R21, R22: 220; R_1206_3216Metric_Pad1.30x1.75mm_HandSolder
R23: 100k; R_1206_3216Metric_Pad1.30x1.75mm_HandSolder
R24: 33k; R_1206_3216Metric_Pad1.30x1.75mm_HandSolder
R31: Joystick; joystickXYButton
R38: 22k; R_1206_3216Metric_Pad1.30x1.75mm_HandSolder
R41: 100; R_1206_3216Metric_Pad1.30x1.75mm_HandSolder
SW1, SW2, SW3, SW4, SW5: SW_Push; SW_PUSH_6mm_H5mm
TP1, TP2, TP7, TP8, TP9, TP10, TP11, TP21, TP22, TP25, TP26, TP27, TP28, TP29, TP33: TestPoint_THTPad_D1.0mm_Drill0.5mm
TP5V1: TP5V; TestPoint_THTPad_D1.0mm_Drill0.5mm
U2: SN65HVD234; SOIC-8_3.9x4.9mm_P1.27mm
U3: STM32F103RETx; LQFP-64_10x10mm_P0.5mm
U4: TPS54302; SOT-23-6
U6: AMS1117-3.3; SOT-223-3_TabPin2
U7: 74HCT04; SO-14_3.9x8.65mm_P1.27mm
Y2: 8MHz; Crystal_SMD_TXC_7M-4Pin_3.2x2.5mm

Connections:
3V3_uC: C56.2, C57.2, C58.2, C59.2, C74.2, C75.1, D15.2 (A), J1.2, J17.1, JP5.3 (B), L12.2, R1.1, R3.1, R5.1, R13.1, R17.1, R31.1 (X1), R31.4 (Y1), R32.1, R35.1, R36.1, R43.1, R45.1, U2.3 (VCC), U3.1 (VBAT), U3.19 (VDD), U3.32 (VDD), U3.48 (VDD), U3.64 (VDD), U6.2 (VO)
5V: C66.2, C67.2, C68.2, C73.2, J1.7, L13.2, R23.1, R41.2, TP5V1.1, U6.3 (VI), U7.14 (VCC)
24V: D13.2 (A), J3.1
24V_P: C69.1, D13.1 (K), Q4.3 (E), Q7.3 (E), R9.2
24V_SWITCHED: C65.2, D2.2 (A), U4.3 (VIN)
/controller/OCS_IN: C62.2, U3.5 (PD0), Y2.1
/controller/OSC_OUT: R15.2, U3.6 (PD1)
BUSWAKE: R6.2, U3.33 (PB12)
CANH: J9.3, JP4.2 (B), Q4.1 (C), U2.7 (CANH)
CANL: J9.2, R2.1, U2.6 (CANL)
CAN_RX: U2.4 (R), U3.44 (PA11)
CAN_TX: U2.1 (D), U3.45 (PA12)
DISPLAY_DC: J1.6, U3.26 (PB0)
DISPLAY_RES: J1.5, U3.27 (PB1)
GND: C1.1, C2.2, C3.2, C56.1, C57.1, C58.1, C59.1, C60.1, C61.1, C62.1, C63.1, C65.1, C66.1, C67.1, C69.2, C73.1, C74.1, C75.2, D1.1 (K), D9.1 (K), D10.1 (K), D11.1 (K), J1.1, J3.2, J4.2, J5.2, J10.1, JP5.1 (A), Q1.3 (S), Q2.3 (S), Q3.3 (S), Q6.3 (E), Q8.3 (E), R12.2, R24.1, R28.1, R29.2, R30.1, R31.3 (X2), R31.6 (Y2), R31.9 (B2), R31.10 (B2.2), R31.11 (GND), R31.12 (GND), R31.13 (GND), R31.14 (GND), R33.2, R38.1, R40.1, SW1.1, SW2.1, SW3.1, SW4.1, SW5.1, U2.2 (GND), U2.8 (Rs), U3.12 (VSSA), U3.18 (VSS), U3.31 (VSS), U3.47 (VSS), U3.60 (BOOT0), U3.63 (VSS), U4.1 (GND), U6.1 (GND), U7.7 (GND), Y2.2, Y2.4
KEEP_ON: R8.2, U3.34 (PB13)
LED2: R19.1, U3.56 (PB4)
LED3: R20.1, U3.57 (PB5)
LED_ALIVE: R18.1, U3.59 (PB7)
unnamed: C63.2, R15.1, Y2.3
unnamed: D1.2 (A), R20.2
unnamed: D2.1 (K), Q7.1 (C)
unnamed: D9.2 (A), R17.2
unnamed: D10.2 (A), R18.2
unnamed: D11.2 (A), R19.2
unnamed: D15.1 (K), R37.2
unnamed: F1.1, Q2.2 (D), Q2.4 (D)
unnamed: F2.1, Q3.2 (D), Q3.4 (D)
unnamed: F3.1, Q1.2 (D), Q1.4 (D)
unnamed: J5.1, R22.2
unnamed: J5.3, R21.2
unnamed: JP1.1 (A), U3.61 (PB8)
unnamed: JP2.1 (A), U3.62 (PB9)
unnamed: JP3.1 (A), U3.29 (PB10)
unnamed: JP4.1 (A), R2.2
unnamed: JP5.2 (C), U2.5 (EN)
unnamed: JP6.2 (B), U3.24 (PC4)
unnamed: JP7.2 (B), U3.25 (PC5)
unnamed: JP8.2 (B), U3.37 (PC6)
unnamed: JP9.2 (B), U3.38 (PC7)
unnamed: Q1.1 (G), U7.12
unnamed: Q2.1 (G), U7.6
unnamed: Q3.1 (G), U7.8
unnamed: Q4.2 (B), R4.2
unnamed: Q6.2 (B), R6.1
unnamed: Q6.1 (C), R4.1
unnamed: Q7.2 (B), R7.2, R9.1, R10.1
unnamed: Q8.2 (B), R8.1
unnamed: Q8.1 (C), R7.1
unnamed: R10.2, R11.2, SW1.2
unnamed: TP7.1, U3.14 (PA0)
unnamed: TP8.1, U3.15 (PA1)
unnamed: TP9.1, U3.16 (PA2)
unnamed: TP10.1, U3.17 (PA3)
unnamed: TP2.1, U3.50 (PA15)
unnamed: TP25.1, U3.28 (PB2)
unnamed: TP1.1, U3.58 (PB6)
unnamed: TP33.1, U3.30 (PB11)
unnamed: TP21.1, U3.39 (PC8)
unnamed: TP22.1, U3.40 (PC9)
unnamed: TP26.1, U3.53 (PC12)
unnamed: TP27.1, U3.2 (PC13)
unnamed: TP28.1, U3.3 (PC14)
unnamed: TP29.1, U3.4 (PC15)
unnamed: TP11.1, U3.54 (PD2)
unnamed: C61.2, L12.1, U3.13 (VDDA)
unnamed: C64.2, U4.6 (BOOT)
unnamed: C68.1, R23.2, R24.2, R38.2, U4.4 (FB)
unnamed: C64.1, L13.1, U4.2 (SW)
unnamed: U7.4, U7.5
unnamed: U7.9, U7.10
unnamed: U7.2, U7.13
OUT1_LS: F1.2, J3.3
OUT2_LS: F2.2, J3.4
OUT3_LS: F3.2, J9.1
OUT_CONTROL1: JP1.2 (B), R29.1, U7.3
OUT_CONTROL2: JP2.2 (B), R30.2, U7.11
OUT_CONTROL3: JP3.2 (B), R33.1, U7.1
SPI1_CLK: J1.3, U3.21 (PA5)
SPI1_MISO: JP11.1 (A), U3.22 (PA6)
SPI1_MOSI: J1.4, U3.23 (PA7)
SPI1_NSS: JP10.1 (A), U3.20 (PA4)
SWCLK: J4.1, U3.49 (PA14)
SWDIO: J4.3, U3.46 (PA13)
SWO: J18.1, U3.55 (PB3)
UART4_RX: R22.1, U3.52 (PC11)
UART4_TX: R21.1, R37.1, U3.51 (PC10)
button1: J11.1, R1.2, R26.1, SW2.2
button2: J11.2, R3.2, R25.1, SW3.2
button3: J11.3, R5.2, R16.1, SW4.2
button4: J11.4, R13.2, R14.1, SW5.2
pot1: J10.2, R27.1
pot2: J10.3, R39.1
pot5V: J10.4, R41.1
switch1: J7.1, R34.1, R35.2
switch2: J7.2, R36.2, R42.1
switch3: J7.3, R43.2, R44.1
switch4: J7.4, R45.2, R46.1
uC_NRST: C60.2, J16.1, U3.7 (NRST)
uC_button1: R26.2, U3.41 (PA8)
uC_button2: R25.2, U3.35 (PB14)
uC_button3: R16.2, U3.36 (PB15)
uC_joystickX: R31.2 (XM), U3.10 (PC2)
uC_joystickY: R31.5 (YM), U3.11 (PC3)
uC_joystickbutton: R31.7 (B1), R31.8 (B1.2), R32.2, U3.42 (PA9)
uC_pot1: C3.1, R27.2, R28.2, U3.8 (PC0)
uC_pot2: C2.1, R39.2, R40.2, U3.9 (PC1)
uC_pwr_button: C1.2, R11.1, R12.1, U3.43 (PA10)
uC_switch1: JP6.1 (A), R34.2
uC_switch2: JP7.1 (A), R42.2
uC_switch3: JP8.1 (A), R44.2
uC_switch4: JP9.1 (A), R46.2

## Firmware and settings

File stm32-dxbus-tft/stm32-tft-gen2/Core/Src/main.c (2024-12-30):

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
/* Includes ------------------------------------------------------------------*/
#include "main.h"

/* USER CODE BEGIN Includes */
//#include "stm32f1xx_hal_can.h"
#include "hardwareAbstraction.h"
#include "scheduler.h"
#include "display.h"
#include "can_lowlayer.h"
#include "can_application.h"
/* USER CODE END Includes */

ADC_HandleTypeDef hadc1;

CAN_HandleTypeDef hcan;

SPI_HandleTypeDef hspi1;
DMA_HandleTypeDef hdma_spi1_tx;

void SystemClock_Config(void);
static void MX_GPIO_Init(void);
static void MX_DMA_Init(void);
static void MX_ADC1_Init(void);
static void MX_CAN_Init(void);
static void MX_SPI1_Init(void);
/**
  * @brief  The application entry point.
  * @retval int
  */
int main(void)
{
  /* MCU Configuration--------------------------------------------------------*/

  /* Reset of all peripherals, Initializes the Flash interface and the Systick. */
  HAL_Init();

  /* Configure the system clock */
  SystemClock_Config();

  /* Initialize all configured peripherals */
  MX_GPIO_Init();
  MX_DMA_Init();
  MX_ADC1_Init();
  MX_CAN_Init();
  MX_SPI1_Init();
  /* USER CODE BEGIN 2 */

  __HAL_RCC_AFIO_CLK_ENABLE();
  __HAL_AFIO_REMAP_SWJ_NOJTAG(); /* to enable the PB4 as GPIO, according to https://community.st.com/t5/stm32-mcus-products/stm32f103-how-to-use-pb4-as-normal-gpio-njtrst-remap-not-working/td-p/382398 */
  setKeepPower(1);
  display_init();
  HAL_ADC_Start(&hadc1); /* start the AD converter */
  can_init();
  scheduler_init(); /* The scheduler_init() shall be the last function in the init sequence, because here starts the timing reference. */
  /* USER CODE END 2 */

  /* Infinite loop */
  /* USER CODE BEGIN WHILE */
  while (1)
  {
    /* USER CODE END WHILE */

    /* USER CODE BEGIN 3 */
	  scheduler_cyclic();
  }
  /* USER CODE END 3 */
}

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


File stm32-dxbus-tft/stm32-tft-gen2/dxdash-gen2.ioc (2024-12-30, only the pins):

Mcu.UserName=STM32F103RETx
PA0-WKUP.Signal=GPIO_Input
PA10.Signal=GPIO_Input
PA11.Signal=CAN_RX
PA12.Signal=CAN_TX
PA5.Signal=SPI1_SCK
PA6.Signal=SPI1_MISO
PA7.Signal=SPI1_MOSI
PA8.Signal=GPIO_Input
PA9.Signal=GPIO_Input
PB0.Signal=GPIO_Output
PB1.Signal=GPIO_Output
PB10.Signal=GPIO_Output
PB11.Signal=GPIO_Output
PB12.Signal=GPIO_Output
PB13.Signal=GPIO_Output
PB14.Signal=GPIO_Input
PB15.Signal=GPIO_Input
PB2.Signal=GPIO_Output
PB3.Signal=GPIO_Output
PB4.Signal=GPIO_Output
PB5.Signal=GPIO_Output
PB6.Signal=GPIO_Output
PB7.Signal=GPIO_Output
PB8.Signal=GPIO_Output
PB9.Signal=GPIO_Output
PC0.Signal=ADCx_IN10
PC1.Signal=ADCx_IN11
PC10.Signal=UART4_TX
PC11.Signal=UART4_RX
PC12.Signal=GPIO_Output
PC2.Signal=ADCx_IN12
PC3.Signal=ADCx_IN13
PC4.Signal=GPIO_Input
PC5.Signal=GPIO_Input
PC6.Signal=GPIO_Input
PC7.Signal=GPIO_Input
PC8.Signal=GPIO_Output
PC9.Signal=GPIO_Output
PD0-OSC_IN.Signal=RCC_OSC_IN
PD1-OSC_OUT.Signal=RCC_OSC_OUT
PD2.Signal=GPIO_Output

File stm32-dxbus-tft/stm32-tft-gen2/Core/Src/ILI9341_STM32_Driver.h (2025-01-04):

#ifndef ILI9341_STM32_DRIVER_H
#define ILI9341_STM32_DRIVER_H

#include "stm32f1xx_hal.h"

extern SPI_HandleTypeDef hspi1;

#define ILI9341_SCREEN_HEIGHT 	240
#define ILI9341_SCREEN_WIDTH 	320

/* PIN Configuration */
#define HSPI_INSTANCE			&hspi1
#define LCD_CS_PORT				GPIOC /* chip select is not used. Just any free pin. */
#define LCD_CS_PIN				GPIO_PIN_15  /* chip select is not used. Just any free pin. */
#define LCD_DC_PORT				GPIOB
#define LCD_DC_PIN				GPIO_PIN_0
#define	LCD_RST_PORT			GPIOB
#define	LCD_RST_PIN				GPIO_PIN_1

#define BURST_MAX_SIZE 			500
#define BLACK      				0x0000
#define NAVY        			0x000F
#define DARKGREEN   			0x03E0
#define DARKCYAN    			0x03EF
#define MAROON      			0x7800
#define PURPLE      			0x780F
#define OLIVE       			0x7BE0
#define LIGHTGREY   			0xC618
#define DARKGREY    			0x7BEF
#define BLUE        			0x001F
#define GREEN       			0x07E0
#define CYAN        			0x07FF
#define RED         			0xF800
#define MAGENTA     			0xF81F
#define YELLOW      			0xFFE0
#define WHITE       			0xFFFF
#define ORANGE      			0xFD20
#define GREENYELLOW 			0xAFE5
#define PINK        			0xF81F

/* colors from https://gist.github.com/Kongduino/36d152c81bbb1214a2128a2712ecdd18 */
#define TFT_ALICEBLUE 0xF7DF
#define TFT_ANTIQUEWHITE 0xFF5A
#define TFT_AQUA 0x07FF
#define TFT_AQUAMARINE 0x7FFA
#define TFT_AZURE 0xF7FF
#define TFT_BEIGE 0xF7BB
#define TFT_BISQUE 0xFF38
#define TFT_BLACK 0x0000 /*   0, 0, 0 */
#define TFT_BLANCHEDALMOND 0xFF59
#define TFT_BLUE 0x001F /*   0, 0, 255 */
#define TFT_BLUEVIOLET 0x895C
#define TFT_BROWN 0xA145
#define TFT_BURLYWOOD 0xDDD0
#define TFT_CADETBLUE 0x5CF4
#define TFT_CHARTREUSE 0x7FE0
#define TFT_CHOCOLATE 0xD343
#define TFT_CORAL 0xFBEA
#define TFT_CORNFLOWERBLUE 0x64BD
#define TFT_CORNSILK 0xFFDB
#define TFT_CRIMSON 0xD8A7
#define TFT_CYAN 0x07FF /*   0, 255, 255 */
#define TFT_DARKBLUE 0x0011
#define TFT_DARKCYAN 0x03EF /*   0, 128, 128 */
#define TFT_DARKCYAN2 0x0451
#define TFT_DARKGOLDENROD 0xBC21
#define TFT_DARKGRAY 0xAD55
#define TFT_DARKGREEN2 0x0320
#define TFT_DARKGREEN 0x03E0 /*   0, 128, 0 */
#define TFT_DARKGREY 0x7BEF /* 128, 128, 128 */
#define TFT_DARKKHAKI 0xBDAD
#define TFT_DARKMAGENTA 0x8811
#define TFT_DARKOLIVEGREEN 0x5345
#define TFT_DARKORANGE 0xFC60
#define TFT_DARKORCHID 0x9999
#define TFT_DARKRED 0x8800
#define TFT_DARKSALMON 0xECAF
#define TFT_DARKSEAGREEN 0x8DF1
#define TFT_DARKSLATEBLUE 0x49F1
#define TFT_DARKSLATEGRAY 0x2A69
#define TFT_DARKTURQUOISE 0x067A
#define TFT_DARKVIOLET 0x901A
#define TFT_DEEPPINK 0xF8B2
#define TFT_DEEPSKYBLUE 0x05FF
#define TFT_DIMGRAY 0x6B4D
#define TFT_DODGERBLUE 0x1C9F
#define TFT_FIREBRICK 0xB104
#define TFT_FLORALWHITE 0xFFDE
#define TFT_FORESTGREEN 0x2444
#define TFT_FUCHSIA 0xF81F
#define TFT_GAINSBORO 0xDEFB
#define TFT_GHOSTWHITE 0xFFDF
#define TFT_GOLD 0xFEA0
#define TFT_GOLDENROD 0xDD24
#define TFT_GRAY 0x8410
#define TFT_GREEN2 0x0400
#define TFT_GREEN 0x07E0 /*   0, 255, 0 */
#define TFT_GREENYELLOW 0xAFE5 /* 173, 255, 47 */
#define TFT_HONEYDEW 0xF7FE
#define TFT_HOTPINK 0xFB56
#define TFT_INDIANRED 0xCAEB
#define TFT_INDIGO 0x4810
#define TFT_IVORY 0xFFFE
#define TFT_KHAKI 0xF731
#define TFT_LAVENDER 0xE73F
#define TFT_LAVENDERBLUSH 0xFF9E
#define TFT_LAWNGREEN 0x7FE0
#define TFT_LEMONCHIFFON 0xFFD9
#define TFT_LIGHTBLUE 0xAEDC
#define TFT_LIGHTCORAL 0xF410
#define TFT_LIGHTCYAN 0xE7FF
#define TFT_LIGHTGOLDENRODYELLOW 0xFFDA
#define TFT_LIGHTGREEN 0x9772
#define TFT_LIGHTGREY 0xC618 /* 192, 192, 192 */
#define TFT_LIGHTGREY2 0xD69A
#define TFT_LIGHTPINK 0xFDB8
#define TFT_LIGHTSALMON 0xFD0F
#define TFT_LIGHTSEAGREEN 0x2595
#define TFT_LIGHTSKYBLUE 0x867F
#define TFT_LIGHTSLATEGRAY 0x7453
#define TFT_LIGHTSTEELBLUE 0xB63B
#define TFT_LIGHTYELLOW 0xFFFC
#define TFT_LIME 0x07E0
#define TFT_LIMEGREEN 0x3666
#define TFT_LINEN 0xFF9C
#define TFT_MAGENTA 0xF81F /* 255, 0, 255 */
#define TFT_MAROON 0x7800 /* 128, 0, 0 */
#define TFT_MAROON2 0x8000
#define TFT_MEDIUMAQUAMARINE 0x6675
#define TFT_MEDIUMBLUE 0x0019
#define TFT_MEDIUMORCHID 0xBABA
#define TFT_MEDIUMPURPLE 0x939B
#define TFT_MEDIUMSEAGREEN 0x3D8E
#define TFT_MEDIUMSLATEBLUE 0x7B5D
#define TFT_MEDIUMSPRINGGREEN 0x07D3
#define TFT_MEDIUMTURQUOISE 0x4E99
#define TFT_MEDIUMVIOLETRED 0xC0B0
#define TFT_MIDNIGHTBLUE 0x18CE
#define TFT_MINTCREAM 0xF7FF
#define TFT_MISTYROSE 0xFF3C
#define TFT_MOCCASIN 0xFF36
#define TFT_NAVAJOWHITE 0xFEF5
#define TFT_NAVY 0x000F /*   0, 0, 128 */
#define TFT_NAVY2 0x0010
#define TFT_OLDLACE 0xFFBC
#define TFT_OLIVE 0x7BE0 /* 128, 128, 0 */
#define TFT_OLIVE2 0x8400
#define TFT_OLIVEDRAB 0x6C64
#define TFT_ORANGE 0xFD20 /* 255, 165, 0 */
#define TFT_ORANGERED 0xFA20
#define TFT_ORCHID 0xDB9A
#define TFT_PALEGOLDENROD 0xEF55
#define TFT_PALEGREEN 0x9FD3
#define TFT_PALETURQUOISE 0xAF7D
#define TFT_PALEVIOLETRED 0xDB92
#define TFT_PAPAYAWHIP 0xFF7A
#define TFT_PEACHPUFF 0xFED7
#define TFT_PERU 0xCC27
#define TFT_PINK 0xF81F
#define TFT_PINK_2 0xFE19
#define TFT_PLUM 0xDD1B
#define TFT_POWDERBLUE 0xB71C
#define TFT_PURPLE 0x780F /* 128, 0, 128 */
#define TFT_PURPLE2 0x8010
#define TFT_RED 0xF800 /* 255, 0, 0 */
#define TFT_ROSYBROWN 0xBC71
#define TFT_ROYALBLUE 0x435C
#define TFT_SADDLEBROWN 0x8A22
#define TFT_SALMON 0xFC0E
#define TFT_SANDYBROWN 0xF52C
#define TFT_SEAGREEN 0x2C4A
#define TFT_SEASHELL 0xFFBD
#define TFT_SIENNA 0xA285
#define TFT_SILVER 0xC618
#define TFT_SKYBLUE 0x867D
#define TFT_SLATEBLUE 0x6AD9
#define TFT_SLATEGRAY 0x7412
#define TFT_SNOW 0xFFDF
#define TFT_SPRINGGREEN 0x07EF
#define TFT_STEELBLUE 0x4416
#define TFT_TAN 0xD5B1
#define TFT_TEAL 0x0410
#define TFT_THISTLE 0xDDFB
#define TFT_TOMATO 0xFB08
#define TFT_TURQUOISE 0x471A
#define TFT_VIOLET 0xEC1D
#define TFT_WHEAT 0xF6F6
#define TFT_WHITE 0xFFFF /* 255, 255, 255 */
#define TFT_WHITESMOKE 0xF7BE
#define TFT_YELLOW 0xFFE0 /* 255, 255, 0 */
#define TFT_YELLOWGREEN 0x9E66

#define SCREEN_VERTICAL_1		0
#define SCREEN_HORIZONTAL_1		1
#define SCREEN_VERTICAL_2		2
#define SCREEN_HORIZONTAL_2		3

void ILI9341_WriteCommand(uint8_t cmd);
void ILI9341_WriteData(uint8_t data);
void ILI9341_WriteBuffer(uint8_t *buffer, uint16_t len);
void ILI9341_Reset(void);
void ILI9341_Enable(void);
void ILI9341_Init(void);
void ILI9341_SetRotation(uint8_t rotation);
void ILI9341_SetAddress(uint16_t x1, uint16_t y1, uint16_t x2, uint16_t y2);
void ILI9341_DrawColor(uint16_t color);
void ILI9341_DrawColorBurst(uint16_t color, uint32_t size);
void ILI9341_FillScreen(uint16_t color);
void ILI9341_DrawPixel(uint16_t x,uint16_t y,uint16_t color);
void ILI9341_DrawRectangle(uint16_t x, uint16_t y, uint16_t width, uint16_t height, uint16_t color);
void ILI9341_DrawHLine(uint16_t x, uint16_t y, uint16_t width, uint16_t color);
void ILI9341_DrawVLine(uint16_t x, uint16_t y, uint16_t height, uint16_t color);
#endif

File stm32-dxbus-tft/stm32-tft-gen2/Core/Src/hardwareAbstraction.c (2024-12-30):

#include "hardwareAbstraction.h"

uint8_t blTP21toggle;
uint8_t blTP22toggle;
uint8_t blTP33toggle;

void setKeepPower(uint8_t on) {
	if (on) {
		HAL_GPIO_WritePin(GPIOB, GPIO_PIN_13, GPIO_PIN_SET); /* keep power on */
	} else {
		HAL_GPIO_WritePin(GPIOB, GPIO_PIN_13, GPIO_PIN_RESET); /* turn power off */
	}
}

void setBusWake(uint8_t on) {
	if (on) {
		HAL_GPIO_WritePin(GPIOB, GPIO_PIN_12, GPIO_PIN_SET); /* keep power on */
	} else {
		HAL_GPIO_WritePin(GPIOB, GPIO_PIN_12, GPIO_PIN_RESET); /* turn power off */
	}
}

void setLED_D11(uint8_t on) {
	if (on) {
		HAL_GPIO_WritePin(GPIOB, GPIO_PIN_4, GPIO_PIN_SET);
	} else {
		HAL_GPIO_WritePin(GPIOB, GPIO_PIN_4, GPIO_PIN_RESET);
	}
}

void setLED_D1(uint8_t on) {
	if (on) {
		HAL_GPIO_WritePin(GPIOB, GPIO_PIN_5, GPIO_PIN_SET);
	} else {
		HAL_GPIO_WritePin(GPIOB, GPIO_PIN_5, GPIO_PIN_RESET);
	}
}

void setLEDAlive(uint8_t on) {
	if (on) {
		HAL_GPIO_WritePin(GPIOB, GPIO_PIN_7, GPIO_PIN_SET);
	} else {
		HAL_GPIO_WritePin(GPIOB, GPIO_PIN_7, GPIO_PIN_RESET);
	}
}

void setOut1(uint8_t on) {
	if (on) {
		HAL_GPIO_WritePin(GPIOB, GPIO_PIN_8, GPIO_PIN_SET);
	} else {
		HAL_GPIO_WritePin(GPIOB, GPIO_PIN_8, GPIO_PIN_RESET);
	}
}

void setOut2(uint8_t on) {
	if (on) {
		HAL_GPIO_WritePin(GPIOB, GPIO_PIN_9, GPIO_PIN_SET);
	} else {
		HAL_GPIO_WritePin(GPIOB, GPIO_PIN_9, GPIO_PIN_RESET);
	}
}

void setOut3(uint8_t on) {
	if (on) {
		HAL_GPIO_WritePin(GPIOB, GPIO_PIN_10, GPIO_PIN_SET);
	} else {
		HAL_GPIO_WritePin(GPIOB, GPIO_PIN_10, GPIO_PIN_RESET);
	}
}

void setOutTP1(uint8_t on) {
	if (on) {
		HAL_GPIO_WritePin(GPIOB, GPIO_PIN_6, GPIO_PIN_SET);
	} else {
		HAL_GPIO_WritePin(GPIOB, GPIO_PIN_6, GPIO_PIN_RESET);
	}
}
void setOutTP33(uint8_t on) {
	if (on) {
		HAL_GPIO_WritePin(GPIOB, GPIO_PIN_11, GPIO_PIN_SET);
	} else {
		HAL_GPIO_WritePin(GPIOB, GPIO_PIN_11, GPIO_PIN_RESET);
	}
}
void setOutTP21(uint8_t on) {
	if (on) {
		HAL_GPIO_WritePin(GPIOC, GPIO_PIN_8, GPIO_PIN_SET);
	} else {
		HAL_GPIO_WritePin(GPIOC, GPIO_PIN_8, GPIO_PIN_RESET);
	}
}
void setOutTP22(uint8_t on) {
	if (on) {
		HAL_GPIO_WritePin(GPIOC, GPIO_PIN_9, GPIO_PIN_SET);
	} else {
		HAL_GPIO_WritePin(GPIOC, GPIO_PIN_9, GPIO_PIN_RESET);
	}
}


/* buttons and switches are low-active. The functions return TRUE if the button is pressed. */
uint8_t getSwitch1(void) {
	return HAL_GPIO_ReadPin(GPIOC, GPIO_PIN_4)==0;
}
uint8_t getSwitch2(void) {
	return HAL_GPIO_ReadPin(GPIOC, GPIO_PIN_5)==0;
}
uint8_t getSwitch3(void) {
	return HAL_GPIO_ReadPin(GPIOC, GPIO_PIN_6)==0;
}
uint8_t getSwitch4(void) {
	return HAL_GPIO_ReadPin(GPIOC, GPIO_PIN_7)==0;
}
uint8_t getButton1(void) {
	return HAL_GPIO_ReadPin(GPIOA, GPIO_PIN_8)==0;
}
uint8_t getButton2(void) {
	return HAL_GPIO_ReadPin(GPIOB, GPIO_PIN_14)==0;
}
uint8_t getButton3(void) {
	return HAL_GPIO_ReadPin(GPIOB, GPIO_PIN_15)==0;
}
uint8_t getButton4(void) {
	return HAL_GPIO_ReadPin(GPIOA, GPIO_PIN_0)==0;
}
uint8_t getJoystickButton(void) {
	return HAL_GPIO_ReadPin(GPIOA, GPIO_PIN_9)==0;
}
uint8_t getPowerButton(void) {
	return HAL_GPIO_ReadPin(GPIOA, GPIO_PIN_10)==0;
}

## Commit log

2024-09-22 docu: added wakeup plots and CAN logs
    [CAN_LightModule_TX_powerOn_differentLights_powerOff.csv, CAN_powerOn_driveForwardRightTurn_stop_changeFrom2to4_driveForwardRightTurn_stop_off.csv]
2024-09-26 stm32 controls the lights
2024-09-30 send wakeup pulse. Send CAN messages. Shortly unlocking the brake.
    [TFT-with-DXCAN.ioc, canbus.c, main.c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]
2024-09-30 steering reacts, motor not
2024-10-03 fix/improvement for joystick simulation
    [canbus.c]
2024-10-04 docu: pictures and motor pinout
2024-10-04 docu: park brake
2024-10-07 added ADC conversion, added logs
    [CAN_powerOn_lightOnWhileLightsDisconnected_SlmErr4_UcmErr2_powerOff.csv, CAN_powerOn_mot2disconnected_MotErr5_UcmErr5.csv, CAN_powerOn_servoDisconnected_SlmErr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]
2024-10-07 fix: correct clock. Feature: read joystick, and control motor and servo with it.
    [TFT-with-DXCAN.ioc, canbus.c, main.c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]
2024-10-08 read buttons. control light and flashers with buttons.
2024-10-09 on/off button works
2024-10-11 flasher buttons cleanup
2024-10-11 state change between driving and standby works. Shutdown works.
    [CAN_powerOn_DriveThreeTimes_powerOff.csv, CAN_powerOn_powerOff_twice.csv]
2024-10-14 prepared simulation of the ServoLightModule
2024-10-15 simulated UCM and simulated SLM are controlling the motor
2024-10-16 docu: added pictures and 3D model, extended readme
    [DXBUS_plug.FCStd, DXBUS_plug.step]
2024-10-22 first draft of dxdash schematic and board
    [Inputs.kicad_sch, controller.kicad_sch, dxdash.kicad_pcb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]
2024-11-12 controller board added features
    [Inputs.kicad_sch, bus.kicad_sch, controller.kicad_sch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]
2024-11-13 added joystick
    [Inputs.kicad_sch, controller.kicad_sch, dxdash.kicad_pcb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]
2024-11-14 added polyfuses
    [controller.kicad_sch, dxdash.kicad_sch, outputdrivers.kicad_sch]
2024-11-15 added screw terminals
    [Inputs.kicad_sch, dxdash.kicad_pcb, spare.kicad_sch]
2024-11-18 added switch inputs. Layout preparation.
    [Inputs.kicad_sch, bus.kicad_sch, controller.kicad_sch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]
2024-11-19 more layout
    [Inputs.kicad_sch, bus.kicad_sch, dxdash.kicad_pcb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]
2024-11-19 layout work in progress
    [dxdash.kicad_pcb, powersupply.kicad_sch]
2024-11-21 board: layout finished
    [bom.csv, controller.kicad_sch, designators.csv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]
2024-12-09 dxdash: corrected some resistor values. Added todos.
    [dxdash.kicad_sch, powersupply.kicad_sch]
2024-12-09 re-arranged STM32 projects into gen1 and gen2
2024-12-09 gen2: integrated hardwareabstraction, scheduler, buttons, powremanager, turnIndicator
    [dxdash.kicad_sch]
2024-12-11 added drivingLight. Routed turn indicators to power outputs.
2024-12-11 added analog inputs. Show analog and buttons on status page.
    [dxdash.kicad_sch]
2024-12-11 all switches and buttons in buttonfield
2024-12-11 added CAN, UCM and SLM. Motor spins, controlled by analog joystick.
2024-12-11 fix double speed of the turn indicator
    [canbus.c]
2024-12-16 gen1: interrupt-driven CAN transmit. PowerModule emulation. Steering works sporadically with emulated PowerModule.
2024-12-29 gen2: interrupt-based CAN transmission. Splash screen.
2024-12-29 gen2: improved TX queue handling
    [2024-12-28_CAN_gen2_run_but_stopped.csv, 2024-12-28_CAN_gen2_run_but_stopped_002.csv]
2024-12-30 gen2: Fix: enable CAN auto-retransmission to avoid message loss. Feature: select creepmode with joystick X
    [dxdash-gen2.ioc, main.c, slm.c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]
2025-01-02 gen2 features: error bar. Drive pedal. Voltage display and lowvoltage detection.
    [can_application.c, display.c, display_pages.c]
2025-01-03 gen2: decode error codes of the PowerModule. Show creepmode and direction.
    [2025-01-03_CAN_gen2_uncoupleG40.csv, 2025-01-03_CAN_original_disconnecting_M1_leads_to_blink5.csv, 2025-01-03_CAN_original_uncoupleG40_leads_to_blink3.csv]
2025-01-04 fix: select unused controller pin for unused chipselect of the display, to avoid out3 flickering.
    [ILI9341_STM32_Driver.h]
2025-01-14 fix: decode network variables of the powermodule independent of their position
    [2025-01-14_CAN_gen2_no_variables_from_powermodule.csv]
2025-01-17 docu: sleep current of the power module

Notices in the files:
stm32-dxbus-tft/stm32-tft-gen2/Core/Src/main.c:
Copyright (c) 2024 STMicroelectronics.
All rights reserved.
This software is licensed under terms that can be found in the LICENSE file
